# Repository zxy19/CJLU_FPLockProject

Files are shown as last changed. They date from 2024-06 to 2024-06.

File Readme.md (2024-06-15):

# CJLU 门锁改装计划
> CJLU_FPLockProject

欢迎阅读此说明。本项目是中国计量大学云莓智能的门锁改装计划项目主项目说明文档。
该项目由若干部分构成，你可以选择你需要的任意部分进行使用。

[TOC]
## 文件结构

```plain
|-assets    markdown相关的资源
|-model     3D模型
|-server    云服务器代码(WIP)
|-src       Ardunio相关功能模块
|-web       网页相关的所有
  |-pages   单片机上存储的一些页面源文件
  |-visitor 访客管理系统(WIP)
|-pcb.zip   嘉立创EDA导出项目
|-test.ino  单片机主项目文件
```

## 物理结构改装与加装

### 改装

物理结构设计上使用的方案最初来自一位网名dome的群友，在此感谢。

**注意：本文提供的方案将需要拆装寝室门锁。对此造成的任何可能的问题，作者不会为你承担任何责任。**

**由于门锁的奇特结构，拆装时请务必两人操作，并妥善保管内外侧门锁**

可行操作流程：

+ 拆下门锁（拆下门锁电池盒内和底部的两颗螺丝）
+ 拆下门锁内连着锁舌的一块结构（锁舌伸出平面的三个螺丝）
+ 位于该结构左上角有一开窗中，穿过一根线，使其能够直接拉动锁舌
+ 从门把手穿孔中穿过xh2.45-6p <=> sh1.00-60线。外侧需要略微留长
+ 将门锁装回，在线引出部分使用小棍或类似物品垫高（有必要可以拆除门内的塑料底板）
+ 测试门是否可以正常关闭，引出的线是否可以正常拉动

至此，改装部分结束，后续结构均不需要更改已有结构。

### 加装

加装部分为两个3D打印件。可以在项目内找到STL和SLDPRT（Solidworks的源文件）。

门外部分用于嵌入一个指纹模块，指纹模块采用的是海凌科HLK-FPM383C（HLK-ZW101为淘宝店家标注的名字，暂时不知道哪个是商品型号）

门内部分用于支撑舵机和单片机及其拓展板。舵机可选MG90,PM10S等。具体尺寸见设计图。单片机拓展版上预留的排母适用于ESP32-C3 supermini开发板。门内的结构可以使用C字形夹紧件固定在门锁上。

拓展板PCB上需要焊接的元件为：2.45-8P排母两个（单片机），XH2.45插座一个（指纹），2.45-3P排针一个（舵机）。推荐同时购买XH2.45延长线。

> PCB 理论上来说还能在这里 [嘉立创社区](https://oshwhub.com/zxypp/esp32_extend_board) 看到（审核没过就不清楚了）

## 门上单片机控制部分

单片机可以在通电时持续按住指纹模块来进入配置模式。配置模式下可以添加指纹，配置无线网络等。配置模式下传感器上蓝色灯光闪烁，此时可以连接到`FingerprintLock`无线网络，并访问http://192.168.4.1/即可进入配置页面。

## 云服务器及其页面（WIP）

## 安装须知

安装完毕所有结构后，请**拆下舵机臂**再通电。通电后待舵机完成转动再安装舵机臂。

进入配置模式，点击调节舵机按钮，**从0开始小幅度增加**调节舵机值（一般最终会调节到一千附近，取决于舵机型号）

在配置模式中，按下添加指纹按钮。观察按钮上的文字。将手指放在传感器上，传感器闪绿色表示成功读取到一次，按钮上的数字会对应增加。当录入完成，手机上弹窗显示“done”

完成后，重新连接电源即可正常使用

## 鸣谢

感谢 Karlcx，去皮的大土豆，dome（QQ名）的支持。感谢室友的理解

欢迎加入云梅不智能群交流门锁折腾 704883666

欢迎fork，issue，pr（但是不保证有时间能处理）

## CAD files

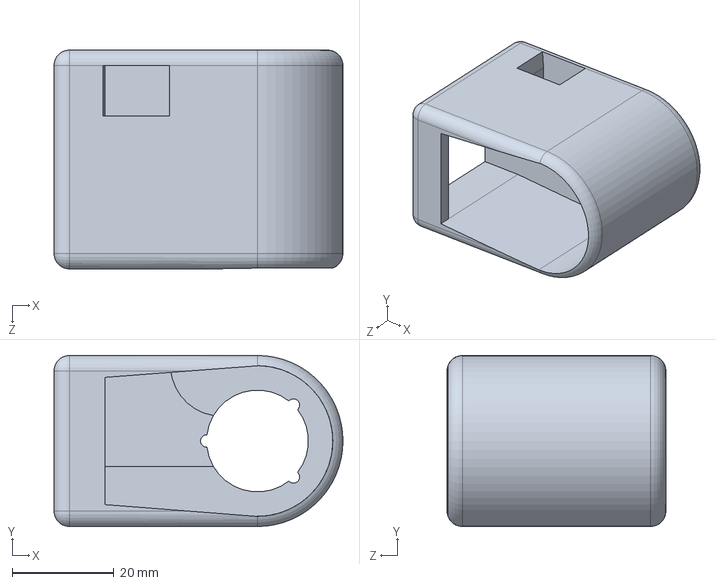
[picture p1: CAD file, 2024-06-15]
model/指纹.SLDPRT
56.8 x 33.6 x 43.0 mm

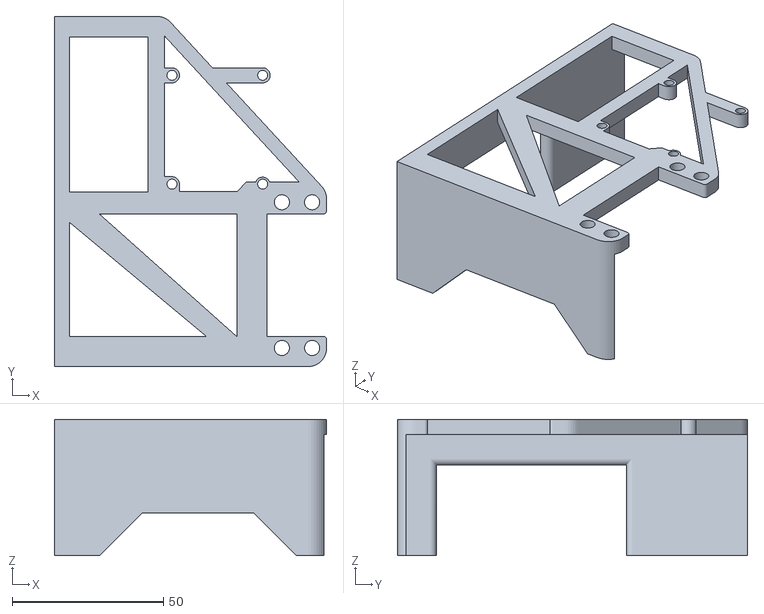
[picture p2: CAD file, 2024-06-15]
model/门内V2E2.STL
90.0 x 115.8 x 45.0

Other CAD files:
model/门内V2.SLDPRT
model/指纹.STL

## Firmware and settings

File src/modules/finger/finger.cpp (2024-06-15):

#include "finger.h"
const char HEAD[] = {0xF1, 0x1F, 0xE2, 0x2E, 0xB6, 0x6B, 0xA8, 0x8A};

uint8_t finger::buffer[100];
uint8_t finger::data[80];
uint32_t finger::lastError;
uint32_t finger::lastDataLen;
void finger::_write(char c) { FINGER_SERIAL.write(c); }
uint8_t finger::_protocol_get_checksum(const uint8_t *data, uint32_t length) {
    uint32_t i = 0;
    uint8_t sum = 0;
    for (i = 0; i < length; i++) {
        sum += data[i];
    }
    return (uint8_t)((~sum) + 1);
}

uint8_t finger::_protocol_get_checksum(uint32_t pass, uint32_t command, const uint8_t *data, uint32_t length) {
    uint32_t i = 0;
    uint8_t sum = 0;
    sum += (pass >> 24) & 0xff;
    sum += (pass >> 16) & 0xff;
    sum += (pass >> 8) & 0xff;
    sum += (pass) & 0xff;
    sum += (command >> 8) & 0xff;
    sum += command & 0xff;
    for (i = 0; i < length; i++) {
        sum += data[i];
    }
    return (uint8_t)((~sum) + 1);
}

void finger::_sendCommand(uint32_t command, const uint8_t *data, uint32_t length) {
    uint8_t tmp[10];
    // send head
    uint32_t len = length + 7;
    tmp[8] = (len >> 8) & 0xff;
    tmp[9] = len & 0xff;
    for (int i = 0; i < 8; i++) {
        _write(HEAD[i]);
        tmp[i] = HEAD[i];
    }
    _write(((len >> 8) & 0xff));
    _write((len & 0xff));
    _write(_protocol_get_checksum(tmp, 10));
    // send command
    // seg_pass
    _write(((PASS >> 24) & 0xff));
    _write(((PASS >> 16) & 0xff));
    _write((PASS >> 8) & 0xff);
    _write((PASS) & 0xff);
    // seg_command
    _write((command >> 8) & 0xff);
    _write(command & 0xff);
    //
    for (int i = 0; i < length; i++) {
        _write(data[i]);
    }

    _write(_protocol_get_checksum(PASS, command, data, length));
}

bool finger::_receive(uint32_t command) {
    uint32_t len = 0, dataLength = 0, totalLen = 0, errorCode = 0;
    bool headOk = false;
    for (int dead = 0; dead != 20; dead++) {
        while (FINGER_SERIAL.available()) {
            uint8_t c = FINGER_SERIAL.read();
            if (!headOk) {     // reading header
                if (len < 8) { // get head
                    if ((char)c == HEAD[len]) {
                        buffer[len] = c;
                        len++;
                        if (len == 8) {
                            totalLen = 0;
                        }
                    } else {
                        len = 0;
                    }
                } else if (len < 10) { // get len
                    buffer[len++] = c;
                    totalLen = (totalLen << 8) | c;
                } else if (len == 10) { // check sum
                    if (_protocol_get_checksum(buffer, len) == c) {
                        headOk = true;
                    } else {
                        headOk = false;
                    }
                    len = 0;
                }
            } else { // reading data
                buffer[len] = c;
                if (len < 4) {
                    if (c == ((PASS >> ((3 - len) * 8)) & 0xff)) {
                        len++;
                    } else
                        len = 0;
                } else if (len < 5) {
                    if (c == ((command >> 8) & 0xff)) {
                        len++;
                    } else
                        len = 0;
                } else if (len < 6) {
                    if (c == (command & 0xff)) {
                        len++;
                    } else
                        len = 0;
                } else if (len < 10) {
                    errorCode = (errorCode << 8) | c;
                    len++;
                } else if (len < totalLen - 1) {
                    data[dataLength++] = c;
                    len++;
                } else {
                    if (_protocol_get_checksum(buffer, len) == c) {
                        lastError = errorCode;
                        lastDataLen = len - 7;
                        return true;
                    } else {
                        len = 0;
                    }
                }
            }
        }
        delay(50);
    }
    lastError = 0xFFFFFF;
    return false;
}
void finger::init() {
    FINGER_SERIAL.begin(57600);
    pinMode(FINGER_INT, INPUT);
    delay(1000);
}
bool finger::isFingerInt() { return digitalRead(FINGER_INT) != 0; }

finger::result_basic finger::CMD_heatBeat() {
    _sendCommand(CODE_CMD_HEART_BEAT, NULL, 0);
    if (_receive(CODE_CMD_HEART_BEAT)) {
        return result_basic(lastError);
    } else {
        return result_basic(0xFFFFFF);
    }
}
finger::result_bool finger::CMD_isFingerOn() {
    _sendCommand(CODE_CMD_IS_FINGER, NULL, 0);
    if (_receive(CODE_CMD_IS_FINGER)) {
        return result_bool(lastError, data[0] != 0);
    } else {
        return result_bool(0xFFFFFF, false);
    }
}
finger::result_basic finger::CMD_reg(uint8_t idx) {
    uint8_t tmp[1] = {idx};
    _sendCommand(CODE_CMD_REG, tmp, 1);
    if (_receive(CODE_CMD_REG)) {
        return result_basic(lastError);
    }
    return result_basic(0xFFFFFF);
}
finger::result_reg finger::CMD_getRegResult() {
    _sendCommand(CODE_CMD_REG_RESULT, NULL, 0);
    if (_receive(CODE_CMD_REG_RESULT)) {
        uint32_t id = data[0];
        id = (id << 8) | data[1];
        return result_reg(lastError, id, data[2]);
    } else {
        return result_reg(0xFFFFFF, 0, 0);
    }
}
finger::result_basic finger::CMD_cancel() {
    _sendCommand(CODE_CMD_CANCEL, NULL, 0);
    if (_receive(CODE_CMD_CANCEL)) {
        return result_basic(lastError);
    } else {
        return result_basic(0xFFFFFF);
    }
}
finger::result_basic finger::CMD_save(uint32_t id) {
    uint8_t tmp[2] = {(id >> 8) & 0xff, id & 0xff};
    _sendCommand(CODE_CMD_SAVE, tmp, 2);
    if (_receive(CODE_CMD_SAVE)) {
        return result_basic(lastError);
    }
    return result_basic(0xFFFFFF);
}
finger::result_id finger::CMD_getSaveResult() {
    _sendCommand(CODE_CMD_SAVE_RESULT, NULL, 0);
    if (_receive(CODE_CMD_SAVE_RESULT)) {
        uint32_t id = data[0];
        id = (id << 8) | data[1];
        return result_id(lastError, id);
    } else {
        return result_id(0xFFFFFF, 0);
    }
}
finger::result_basic finger::CMD_setLed(uint8_t mode, uint8_t color, uint8_t a1, uint8_t a2, uint8_t a3) {
    uint8_t tmp[5] = {mode, color, a1, a2, a3};
    _sendCommand(CODE_CMD_LED, tmp, 5);
    if (_receive(CODE_CMD_LED)) {
        return result_basic(lastError);
    } else {
        return result_basic(0xFFFFFF);
    }
}

void finger::CMD_autoReg(uint8_t waitFinger, uint8_t pressTimes, uint32_t id) {
    uint8_t tmp[4] = {waitFinger, pressTimes, (id >> 8) & 0xff, id & 0xff};
    _sendCommand(CODE_CMD_AUTO_REG, tmp, 4);
}

finger::result_reg_auto finger::CMD_getRegAutoResult() {
    if (_receive(CODE_CMD_AUTO_REG)) {
        uint32_t id = data[1];
        id = (id << 8) | data[2];
        return result_reg_auto(lastError, id, data[3], data[0]);
    }
}
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

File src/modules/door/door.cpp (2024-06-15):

#include "door.h"
#include "../network/network.h"
#include "../preferences/preferences.h"
Servo door::servo;
int door::closeCountdown = 0;
bool door::opened = false;
int door::servoOpen = 0;
void door::open(int time = -1) {
    opened = true;
    servo.writeMicroseconds(door::servoOpen);
    if (time != -1)
        closeCountdown = time;
}
void door::close() {
    opened = false;
    network::send("door", "close");
    servo.writeMicroseconds(door::servoClose);
}

void door::init() {
    servo.attach(door::servoPin);
    servo.writeMicroseconds(door::servoClose);
    servoOpen = preferences::get("servoOpen").toInt();
}
void door::testServoOpen(int openValue){
    servo.writeMicroseconds(openValue);
    servoOpen = openValue;
    preferences::set("servoOpen",String(openValue));
}
void door::loop() {
    if (closeCountdown > 0) {
        closeCountdown--;
        if (closeCountdown == 0)
            close();
    }
}
bool door::isOpen() {
    network::send("door", "open");
    return opened;
}
